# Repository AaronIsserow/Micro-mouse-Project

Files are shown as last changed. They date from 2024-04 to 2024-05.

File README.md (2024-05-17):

# Micro-mouse Project
This project consists of designing an autonomous maze solving robot. This robot is designed to autonomously navigate through a maze environment.
This repository contains the designs of the following two subsystems that are part of the micro-mouse system:
- The power subsystem
- The sensing subsystem

## Micro-Mouse Power Subsystem
The design and documentation for the power subsystem of a functional micro-mouse is provided. The project focuses on designing and manufacturing a power module that meets the specific requirements outlined in the project brief.
The power subsystem is one of several subsystems that make up the micro-mouse, and it is responsible for distributing power from the battery source to the rest of the system.

### Scope
The scope of this project includes:

- Designing and manufacturing a power module that adheres to the project requirements.
- Distributing power from the battery source to the motors and other components.
- Designing the module to accommodate charging from an external source.
- Ensuring the power module fits within the physical constraints of the micro-mouse.
- Testing the power module thoroughly before integration with the rest of the system.

## Micro-Mouse Sensing Subsystem

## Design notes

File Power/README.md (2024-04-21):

# Micro-Mouse Power Subsystem
This repository contains the design and documentation for the power subsystem of a functional micro-mouse, a maze-solving robot. The project focuses on designing and manufacturing a power module that meets the specific requirements outlined in the project brief.

## Project Overview
The micro-mouse project involves the development, testing, and operation of a fully assembled and functioning maze-solving robot. This robot is designed to autonomously navigate through a maze environment. The power subsystem is one of several subsystems that make up the micro-mouse, and it is responsible for distributing power from the battery source to the rest of the system.

## Scope
The scope of this project includes:

- Designing and manufacturing a power module that adheres to the project requirements.
- Distributing power from the battery source to the motors and other components.
- Designing the module to accommodate charging from an external source.
- Ensuring the power module fits within the physical constraints of the micro-mouse.
- Testing the power module thoroughly before integration with the rest of the system.

## Project Focus
This repository specifically focuses on documenting the design of the power subsystem.

## Repository Structure
- Datasheets: Contains the datasheets of all the ICs used.
- KiCAD Design: Contains files related to the design of the circuit diagram and printed circuit board for the power module.
- Production Files: Contains all production files required to order the PCB from JLCPCB
- Project Description: This is the outline of the project given to us

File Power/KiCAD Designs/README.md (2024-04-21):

# KiCAD Designs
This folder includes all design files including
- KiCAD project file
- KiCAD schematic file
- KiCAD pcb file
- Production Files
- Additional component libraries

## Production Files
This subfolder includes all files needed to manufacture the pcb from JLCPCB

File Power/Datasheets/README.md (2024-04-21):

# Datasheets
This folder includes the datasheets used for the final deisgn of the Power Subsystem

- DRV8833 Dual H-Bridge Motor Driver Module
- TP4056 Li-Po battery Chargin Module
- PS-5850A Push Button Switch

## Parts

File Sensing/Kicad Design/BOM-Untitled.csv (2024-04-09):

Comment | Designator | Footprint | LCSC
2.7k | R14,R3,R8 | R_0805_2012Metric | C17530
680 | R13,R2,R7 | R_0603_1608Metric | C23228
75k | R1,R11,R17 | R_0603_1608Metric | C23242
10 | R10,R16,R6 | R_0402_1005Metric | C25077
47k | R12,R18,R5 | R_0603_1608Metric | C25819
PD333-3B/H0/L2 | LED1,LED2,LED3 | LED_PD333_EVE | C264286
2N3904 | Q1,Q2,Q3 | TO-92_Inline | C2874602
100n | C2,C4,C6 | C_0402_1005Metric | C307331
1.8k | R15,R4,R9 | R_0603_1608Metric | C4177
220n | C1,C3,C5 | C_0805_2012Metric | C5378
TSAL4400 | D2,D3,D5 | LED_D3.0mm_IRBlack | C94135

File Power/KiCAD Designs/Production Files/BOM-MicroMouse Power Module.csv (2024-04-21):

Comment | Designator | Footprint | LCSC
10u | C2,C4,C5 | C_0805_2012Metric | C15850
1n | C6,C7 | C_0603_1608Metric | C1588
1k | R3,R4 | R_0805_2012Metric | C17513
Discharge Current Blocked | D3 | D_SOD-323 | C191023
1.5k | R7 | R_0603_1608Metric | C22843
Charging LED (R) | D1 | LED_0603_1608Metric | C2286
1M | R10,R11,R12,R5,R6,R8 | R_0603_1608Metric | C22935
Charged LED (G) | D2 | LED_0805_2012Metric | C2297
47k | R1 | R_0402_1005Metric | C25792
200k | R9 | R_0603_1608Metric | C25811
3k | R2 | R_0603_1608Metric | C4211
DRV8833PWP | U1 | HTSSOP-16-1EP_4.4x5mm_P0.65mm_EP3.4x5mm | C50506
TP4056 | U2 | SOP8-PP_TPW | C5311018
10n | C3 | C_0603_1608Metric | C57112
ON/OFF Switch | SW1 | PS-5850A_GSW | C963201
2.2u | C1 | C_0805_2012Metric

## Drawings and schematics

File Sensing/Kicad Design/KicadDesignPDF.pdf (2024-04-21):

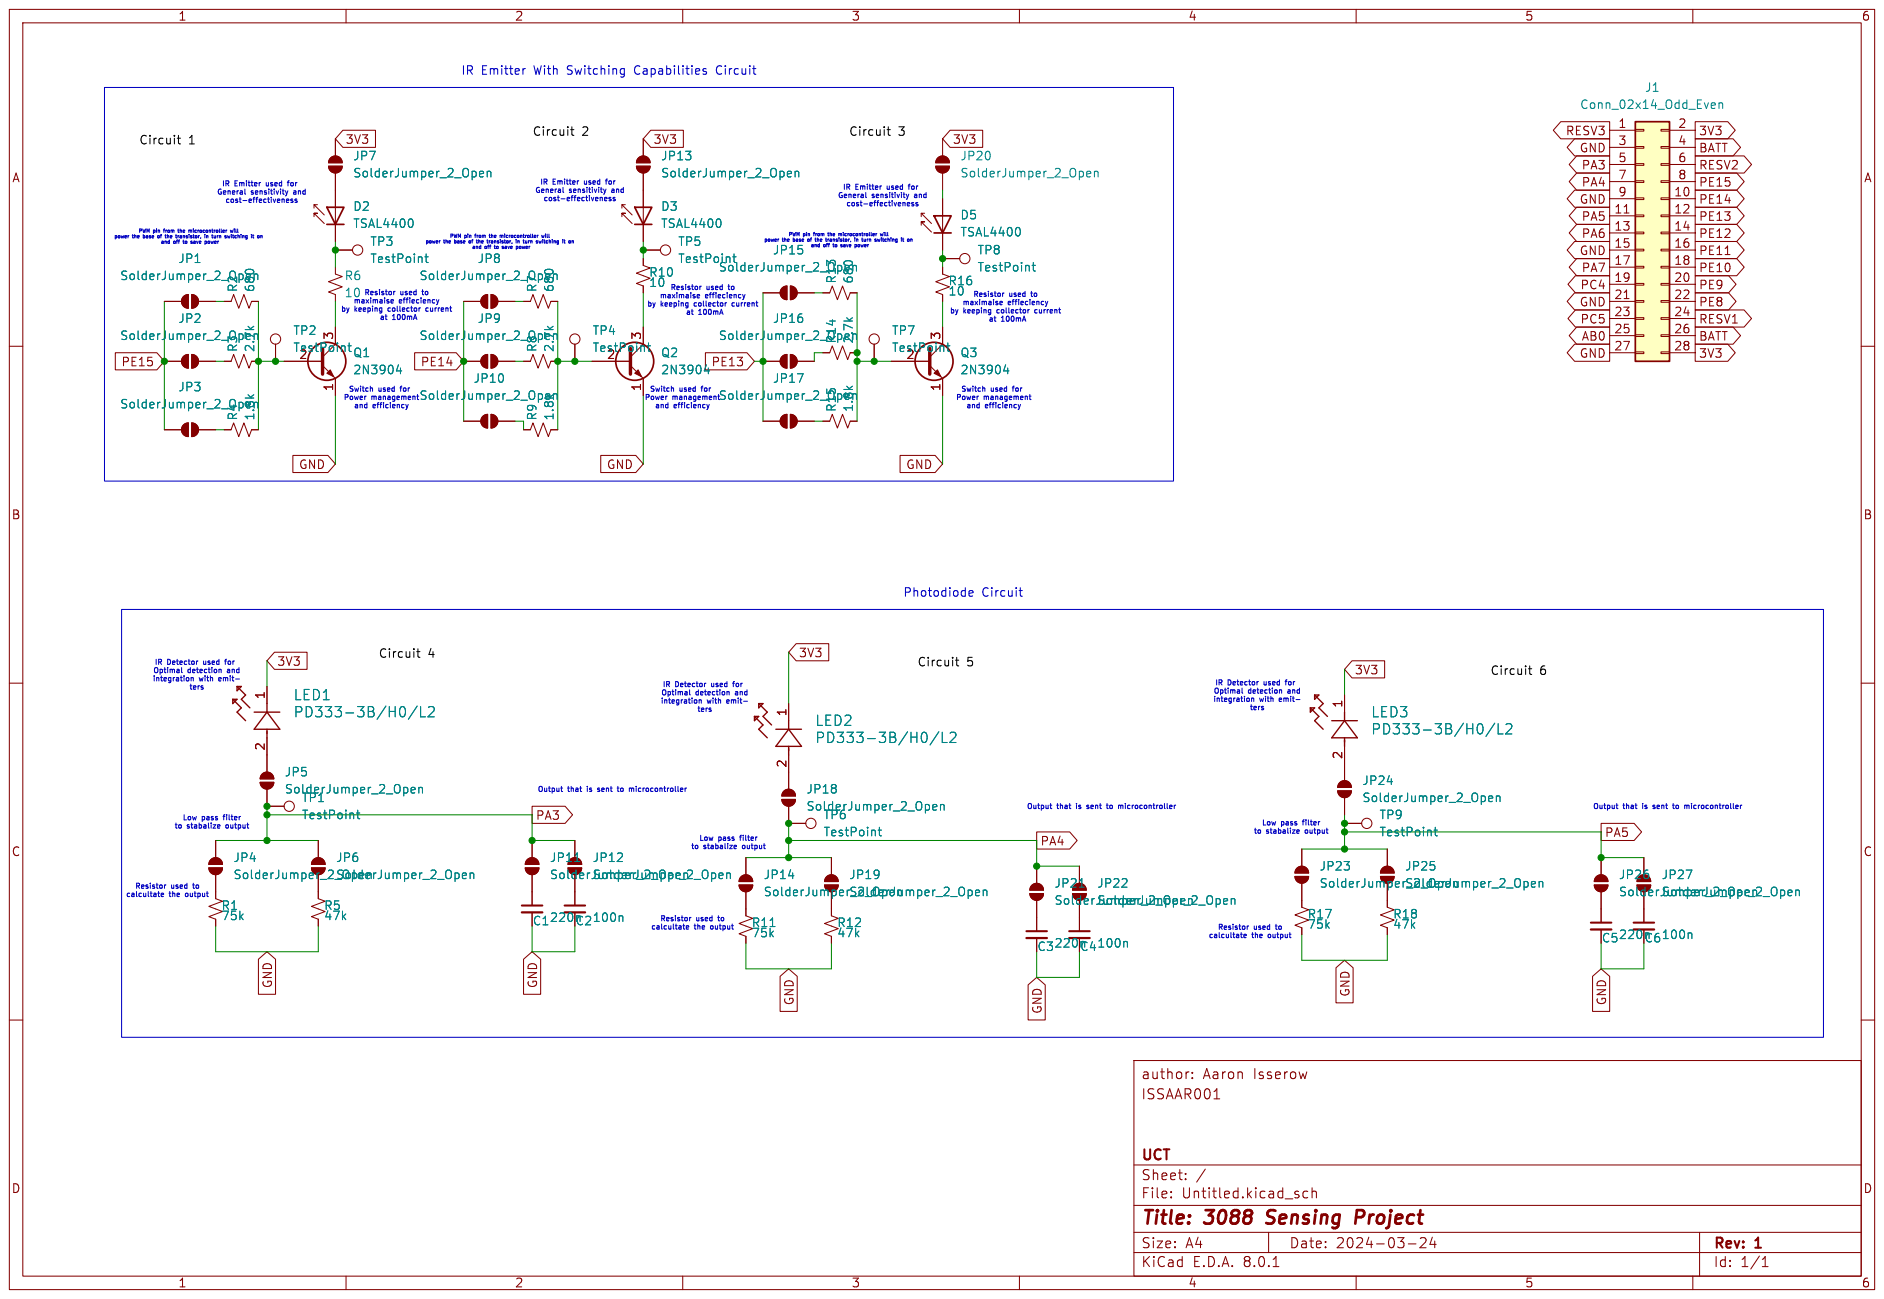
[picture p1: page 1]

Switch used for Power management and efficiency

Switch used for Power management and efficiency JP18 SolderJumper_2_Open LED2 PD333-3B/H0/L2

ters Low pass filter

Id: 1/1 Title: 3088 Sensing Project File: Untitled.kicad_sch Sheet: / UCT

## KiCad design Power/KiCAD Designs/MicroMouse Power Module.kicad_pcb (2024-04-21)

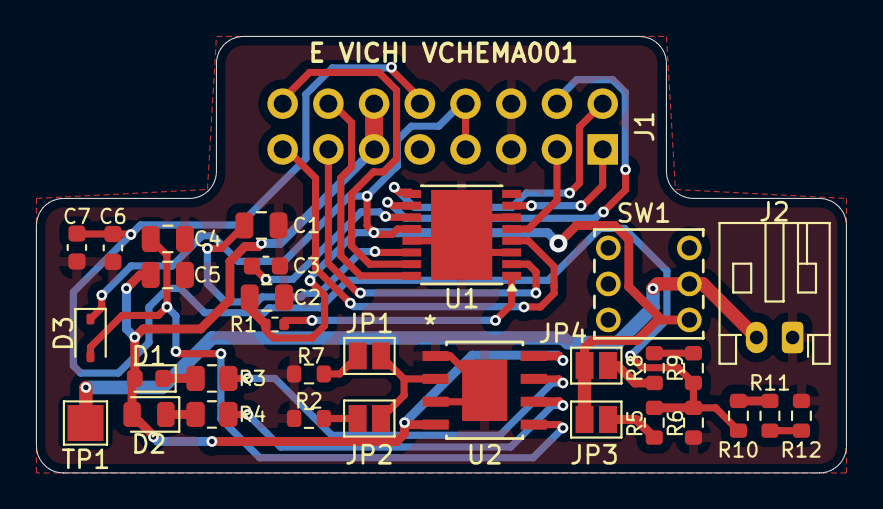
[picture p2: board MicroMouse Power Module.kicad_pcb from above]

Board: 2 copper layers, 45.0 x 24.2 mm, 32 parts (1 on the bottom side), 29 nets.

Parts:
C1: 2.2u; C_0805_2012Metric
C2, C4, C5: 10u; C_0805_2012Metric
C3: 10n; C_0603_1608Metric
C6, C7: 1n; C_0603_1608Metric
D1: Charging LED (R); LED_0603_1608Metric
D2: Charged LED (G); LED_0805_2012Metric
D3: Discharge Current Blocked; D_SOD-323
J1: Electrical pinout; PinHeader_2x08_P2.54mm_Vertical
J2: Battery Pins; JST_PH_S2B-PH-K_1x02_P2.00mm_Horizontal
JP1, JP2, JP3, JP4: SolderJumper-2_P1.3mm_Open_Pad1.0x1.5mm
R1: 47k; R_0402_1005Metric
R2: 3k; R_0603_1608Metric
R3, R4: 1k; R_0805_2012Metric
R5, R6, R8, R10, R11, R12: 1M; R_0603_1608Metric
R7: 1.5k; R_0603_1608Metric
R9: 200k; R_0603_1608Metric
SW1: ON/OFF Switch; PS-5850A_GSW
TP1: Battery check; TestPoint_Pad_2.0x2.0mm
U1: DRV8833PWP; HTSSOP-16-1EP_4.4x5mm_P0.65mm_EP3.4x5mm
U2: TP4056; SOP8-PP_TPW

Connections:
+3.7V: C2.1, D3.1 (K), J1.7, J1.8, JP3.1 (A), JP4.2 (B), R1.1, SW1.6 (C), U1.12 (VM)
+5V: C5.1, D1.2 (A), D2.2 (A), J1.11, J1.12, U2.4 (VCC), U2.8 (CE)
/+: J2.2, SW1.5 (B), TP1.1
/BATT_ADC: C6.1, C7.1, J1.10, R5.1, R6.2, R9.1, R10.2
/Motor1_A: J1.13, U1.2 (AOUT1)
/Motor1_B: J1.15, U1.4 (AOUT2)
/Motor2_A: J1.1, U1.7 (BOUT1)
/Motor2_B: J1.3, U1.5 (BOUT2)
/PWM1: J1.2, U1.9 (BIN1)
/PWM2: J1.4, U1.10 (BIN2)
/PWM3: J1.14, U1.16 (AIN1)
/PWM4: J1.16, U1.15 (AIN2)
GND: C1.2, C2.2, C3.1, C4.2, C5.2, C6.2, C7.2, J1.5, J1.6, J2.1, R2.1, R6.1, R7.1, R12.1, U1.3 (AISEN), U1.6 (BISEN), U1.13 (GND), U1.17 (GND), U2.1 (TEMP), U2.3 (GND), U2.EPAD
unnamed: D1.1 (K), R3.2
unnamed: D2.1 (K), R4.2
unnamed: C4.1, D3.2 (A), U2.5 (BAT)
unnamed: JP1.1 (A), R7.2
unnamed: JP1.2 (B), JP2.2 (B), U2.2 (PROG)
unnamed: JP2.1 (A), R2.2
unnamed: JP3.2 (B), R5.2
unnamed: JP4.1 (A), R8.2
unnamed: R8.1, R9.2
unnamed: R10.1, R11.2
unnamed: R11.1, R12.2
unnamed: C3.2, U1.11 (VCP)
unnamed: C1.1, U1.14 (VINT)
unnamed: R1.2, U1.1 (~SLEEP)
unnamed: R3.1, U2.7 (*CHRG)
unnamed: R4.1, U2.6 (*STDBY)

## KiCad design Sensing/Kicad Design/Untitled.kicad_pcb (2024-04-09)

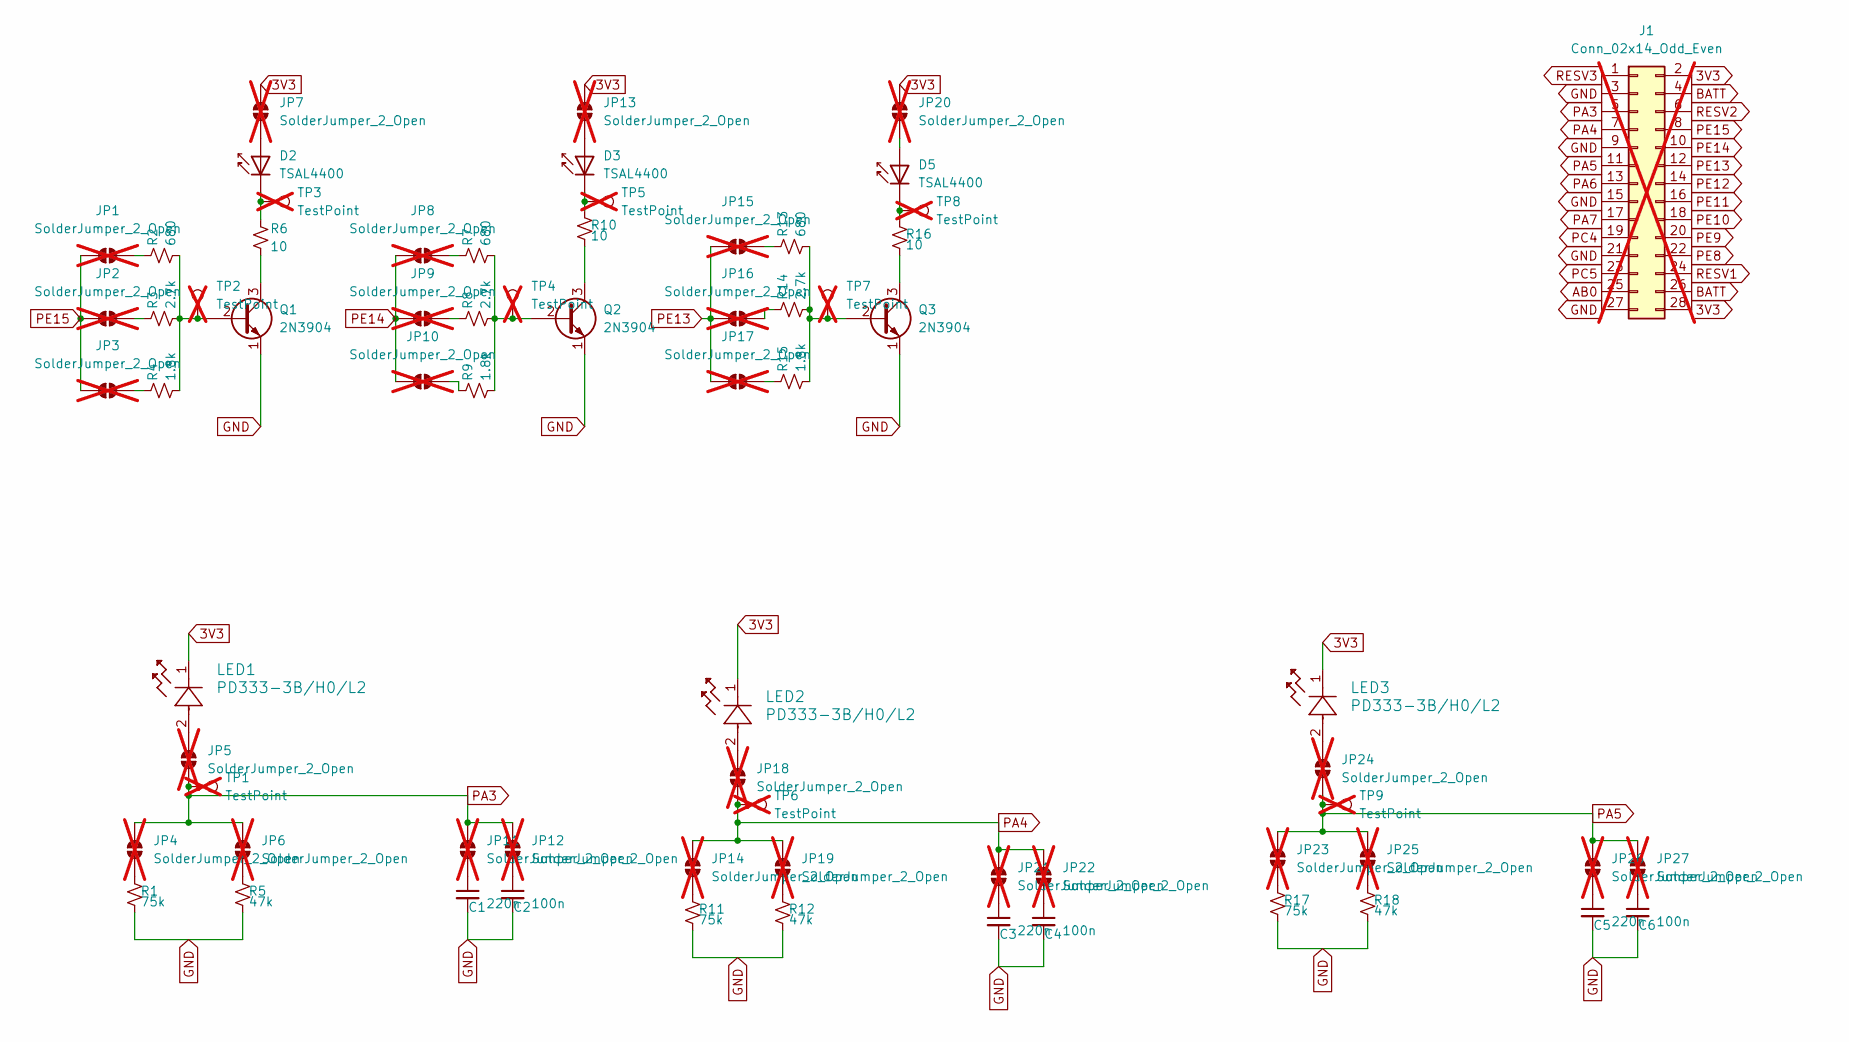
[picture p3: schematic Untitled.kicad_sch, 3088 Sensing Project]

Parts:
C1, C3, C5: 220n; C_0805_2012Metric; LCSC C5378
C2, C4, C6: 100n; C_0402_1005Metric; LCSC C307331
D2, D3, D5: TSAL4400; LED_D3.0mm_IRBlack; LCSC C94135
J1: Conn_02x14_Odd_Even; PinHeader_2x14_P2.54mm_Vertical; not fitted
JP1, JP2, JP3, JP4, JP5, JP6, JP7, JP8, JP9, JP10, JP11, JP12, JP13, JP14, JP15, JP16, JP17, JP18, JP19, JP20, JP21, JP22, JP23, JP24, JP25, JP26, JP27: SolderJumper_2_Open; SolderJumper-2_P1.3mm_Open_Pad1.0x1.5mm; not fitted
LED1, LED2, LED3: PD333-3B/H0/L2; LED_PD333_EVE; LCSC C264286
Q1, Q2, Q3: 2N3904; TO-92_Inline; LCSC C2874602
R1, R11, R17: 75k; R_0603_1608Metric; LCSC C23242
R2, R7, R13: 680; R_0603_1608Metric; LCSC C23228
R3, R8, R14: 2.7k; R_0805_2012Metric; LCSC C17530
R4, R9, R15: 1.8k; R_0603_1608Metric; LCSC C4177
R5, R12, R18: 47k; R_0603_1608Metric; LCSC C25819
R6, R10, R16: 10; R_0402_1005Metric; LCSC C25077
TP1, TP2, TP3, TP4, TP5, TP6, TP7, TP8, TP9: TestPoint; TestPoint_Pad_D2.0mm; not fitted

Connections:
3V3: J1.2, J1.28, JP7.1 (A), JP13.1 (A), JP20.1 (A), LED1.1, LED2.1, LED3.1
AB0: J1.25
BATT: J1.4, J1.26
GND: C1.2, C2.2, C3.2, C4.2, C5.2, C6.2, J1.3, J1.9, J1.15, J1.21, J1.27, Q1.1 (E), Q2.1 (E), Q3.1 (E), R1.2, R5.2, R11.2, R12.2, R17.2, R18.2
unnamed: D2.2 (A), JP7.2 (B)
unnamed: D2.1 (K), R6.1, TP3.1
unnamed: D3.2 (A), JP13.2 (B)
unnamed: D3.1 (K), R10.1, TP5.1
unnamed: D5.2 (A), JP20.2 (B)
unnamed: D5.1 (K), R16.1, TP8.1
unnamed: JP1.1 (A), R2.1
unnamed: JP2.1 (A), R3.1
unnamed: JP3.1 (A), R4.1
unnamed: JP4.1 (A), R1.1
unnamed: JP5.1 (A), LED1.2
unnamed: JP6.1 (A), R5.1
unnamed: JP8.1 (A), R7.1
unnamed: JP9.1 (A), R8.1
unnamed: JP10.1 (A), R9.1
unnamed: C1.1, JP11.1 (A)
unnamed: C2.1, JP12.1 (A)
unnamed: JP14.1 (A), R11.1
unnamed: JP15.1 (A), R13.1
unnamed: JP16.1 (A), R14.1
unnamed: JP17.1 (A), R15.1
unnamed: JP18.1 (A), LED2.2
unnamed: JP19.1 (A), R12.1
unnamed: C3.1, JP21.1 (A)
unnamed: C4.1, JP22.1 (A)
unnamed: JP23.1 (A), R17.1
unnamed: JP24.1 (A), LED3.2
unnamed: JP25.1 (A), R18.1
unnamed: C5.1, JP26.1 (A)
unnamed: C6.1, JP27.1 (A)
unnamed: Q1.2 (B), R2.2, R3.2, R4.2, TP2.1
unnamed: Q1.3 (C), R6.2
unnamed: Q2.2 (B), R7.2, R8.2, R9.2, TP4.1
unnamed: Q2.3 (C), R10.2
unnamed: Q3.2 (B), R13.2, R14.2, R15.2, TP7.1
unnamed: Q3.3 (C), R16.2
PA3: J1.5, JP4.2 (B), JP5.2 (B), JP6.2 (B), JP11.2 (B), JP12.2 (B), TP1.1
PA4: J1.7, JP14.2 (B), JP18.2 (B), JP19.2 (B), JP21.2 (B), JP22.2 (B), TP6.1
PA5: J1.11, JP23.2 (B), JP24.2 (B), JP25.2 (B), JP26.2 (B), JP27.2 (B), TP9.1
PA6: J1.13
PA7: J1.17
PC4: J1.19
PC5: J1.23
PE8: J1.22
PE9: J1.20
PE10: J1.18
PE11: J1.16
PE12: J1.14
PE13: J1.12, JP15.2 (B), JP16.2 (B), JP17.2 (B)
PE14: J1.10, JP8.2 (B), JP9.2 (B), JP10.2 (B)
PE15: J1.8, JP1.2 (B), JP2.2 (B), JP3.2 (B)
RESV1: J1.24
RESV2: J1.6
RESV3: J1.1

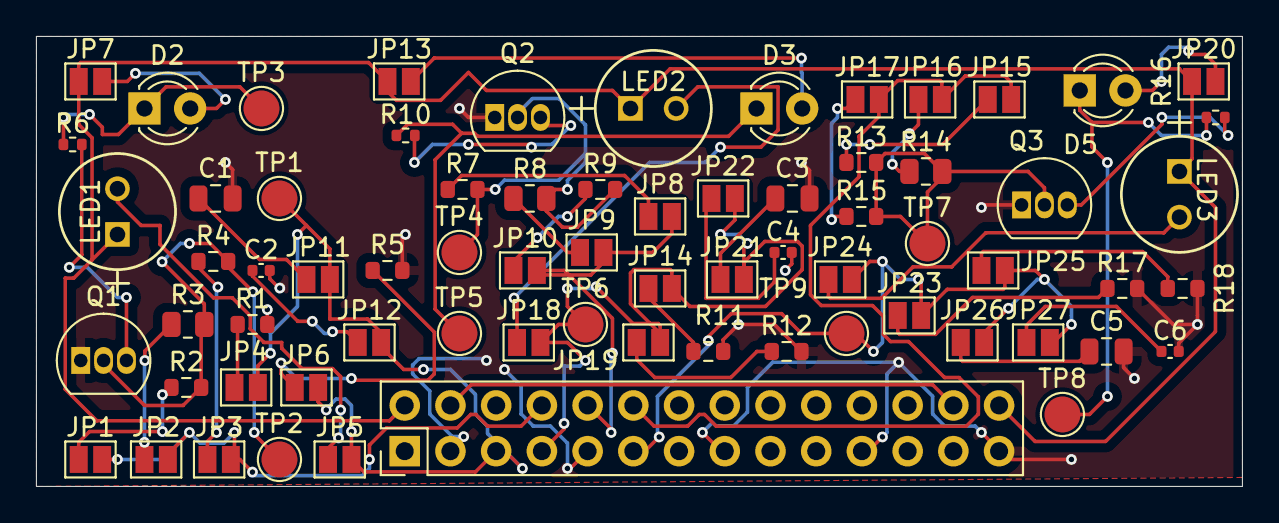
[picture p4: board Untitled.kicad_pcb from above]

Board: 2 copper layers, 67.0 x 25.0 mm, 70 parts (0 on the bottom side), 45 nets.

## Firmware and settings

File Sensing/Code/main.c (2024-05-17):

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
/* Includes ------------------------------------------------------------------*/
#include "main.h"
#include "adc.h"
#include "tim.h"
#include "gpio.h"

/* USER CODE BEGIN Includes */
#define freq 1000
#define dc 10
/* USER CODE END Includes */


/* USER CODE BEGIN PV */
//JUSTIN - START 1/3
uint16_t adc_value1,adc_value2,adc_value3;
uint8_t channel = 0;
//JUSTIN - END
/* USER CODE END PV */

void SystemClock_Config(void);
/**
  * @brief  The application entry point.
  * @retval int
  */
int main(void)
{
  /* MCU Configuration--------------------------------------------------------*/

  /* Reset of all peripherals, Initializes the Flash interface and the Systick. */
  HAL_Init();

  /* Configure the system clock */
  SystemClock_Config();

  /* Initialize all configured peripherals */
  MX_GPIO_Init();
  MX_ADC_Init();
  MX_TIM1_Init();
  /* USER CODE BEGIN 2 */
  HAL_TIM_PWM_Start(&htim1,TIM_CHANNEL_1);

  /* USER CODE END 2 */

  /* Infinite loop */
  /* USER CODE BEGIN WHILE */
  while (1)
  {
    /* USER CODE END WHILE */

    /* USER CODE BEGIN 3 */
    //JUSTIN - START 2/3
    ADC1->CHSELR = ADC_CHSELR_CHSEL3;
    HAL_Delay(1);
    HAL_ADC_Start(&hadc);
    while(HAL_ADC_PollForConversion(&hadc,5)!= HAL_OK);
    adc_value1 = HAL_ADC_GetValue(&hadc);
    HAL_ADC_Stop(&hadc);
    if(adc_value1 >= 2300) {
      HAL_GPIO_WritePin(LED7_GPIO_Port,LED7_Pin,SET);
    } else if (adc_value1 <= 2000){
      HAL_GPIO_WritePin(LED7_GPIO_Port,LED7_Pin,RESET);
    }
    
    ADC1->CHSELR = ADC_CHSELR_CHSEL4;
    HAL_Delay(1);
    HAL_ADC_Start(&hadc);
    while(HAL_ADC_PollForConversion(&hadc,5)!= HAL_OK);
    adc_value2 = HAL_ADC_GetValue(&hadc);
    HAL_ADC_Stop(&hadc);
    if(adc_value2 >= 1700) {
      HAL_GPIO_WritePin(LED7_GPIO_Port,LED6_Pin,SET);
    } else if (adc_value2 <= 1500) {
      HAL_GPIO_WritePin(LED7_GPIO_Port,LED6_Pin,RESET);
    }
    
    ADC1->CHSELR = ADC_CHSELR_CHSEL7;
    HAL_Delay(1);
    HAL_ADC_Start(&hadc);
    while(HAL_ADC_PollForConversion(&hadc,5)!= HAL_OK);
    adc_value3 = HAL_ADC_GetValue(&hadc);
    HAL_ADC_Stop(&hadc);
    if(adc_value3 >= 1700) {
      HAL_GPIO_WritePin(LED7_GPIO_Port,LED5_Pin,SET);
    } else if (adc_value2 <= 1500){
      HAL_GPIO_WritePin(LED7_GPIO_Port,LED5_Pin,RESET);
    }
    
    //JUSTIN - END
  }
  /* USER CODE END 3 */
}

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
/* USER CODE BEGIN 4 */
//JUSTIN - START 3/3
/* I took this code from the adc.c file - In the init section.
* Regrettably setting up the ADC for reading multiple channels is not great without using DMA (scary)
* So you would need to just look at that file and work out how to modify your set channel accordingly.
*/
void adc_set_channel(uint8_t num) {
    ADC_ChannelConfTypeDef sConfig = {0};

    if (num>0) {
      sConfig.Channel = ADC_CHANNEL_5;
    } else {
      sConfig.Channel = ADC_CHANNEL_6;
    }
    sConfig.Rank = ADC_RANK_CHANNEL_NUMBER;
    sConfig.SamplingTime = ADC_SAMPLETIME_1CYCLE_5;
    if (HAL_ADC_ConfigChannel(&hadc, &sConfig) != HAL_OK)
    {
      Error_Handler();
    }
}
//JUSTIN - END
/* USER CODE END 4 */
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


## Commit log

2024-04-21 Update and rename Power/KiCAD Designs/BOM-MicroMouse Power Module.csv to Power/KiCAD Designs/Production Files/BOM-MicroMouse Power Module.csv
    [BOM-MicroMouse Power Module.csv]
2024-04-21 Update and rename Power/KiCAD Designs/CPL-MicroMouse Power Module.csv to Power/KiCAD Designs/Production Files/CPL-MicroMouse Power Module.csv
    [CPL-MicroMouse Power Module.csv]
2024-04-21 Rename Power/KiCAD Designs/GERBER-MicroMouse Power Module.zip to Power/KiCAD Designs/Production Files/GERBER-MicroMouse Power Module.zip

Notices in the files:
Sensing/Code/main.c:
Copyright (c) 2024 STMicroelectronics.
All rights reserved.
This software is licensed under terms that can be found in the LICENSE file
